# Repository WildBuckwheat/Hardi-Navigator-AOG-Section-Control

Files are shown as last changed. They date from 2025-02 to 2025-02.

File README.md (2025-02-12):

# Note

This project is a work in progress. Progress notes are shared below.

# Hardi-Navigator-AOG-Section-Control

 A PCB that adds AgOpenGPS section and rate control functionality to a Hardi Navigator 3000 trailed sprayer. This PCB replaces a PCB installed on the sprayer from the factory. No cutting of wires is required to install the new PCB and the sprayer can quickly be reverted to factory operation. Based very heavily on SK21's RC15 PCB.

 ## The Sprayer

 The sprayer is a Hardi Navigator 3000. This sprayer is generally by a John Deere 7410 tractor equipped with an AgOpenGPS guidance system. In the past this tractor was equipped with a Trimble CFX-750 and the Hardi JobCom connection was used for automatic section control. Since upgrading to AgOpenGPS the sections have been controlled manually. The intent of this project is to regain automatic section control.

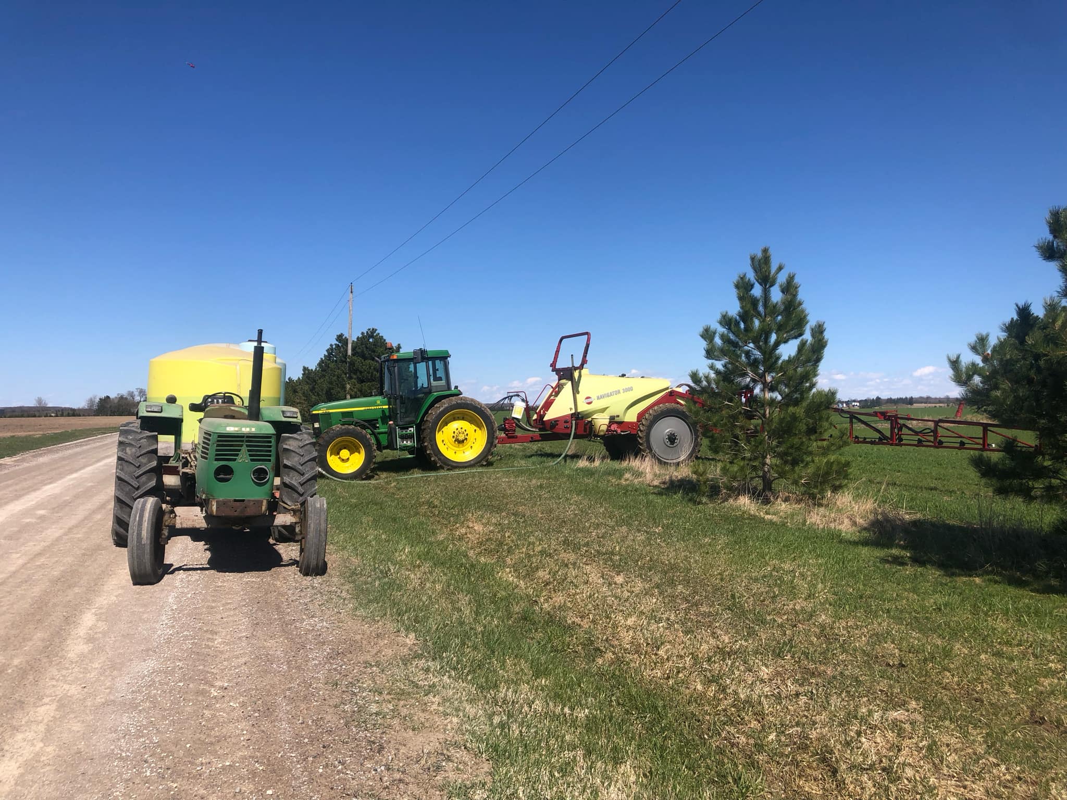
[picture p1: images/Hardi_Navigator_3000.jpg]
Hardi Navigator 3000
  

 The sprayer is equipped with a 90' eagle boom and 6 section valves. The 6 section valves are of the EVC type, utilizing a DC motor to direct flow between the boom and tank return.

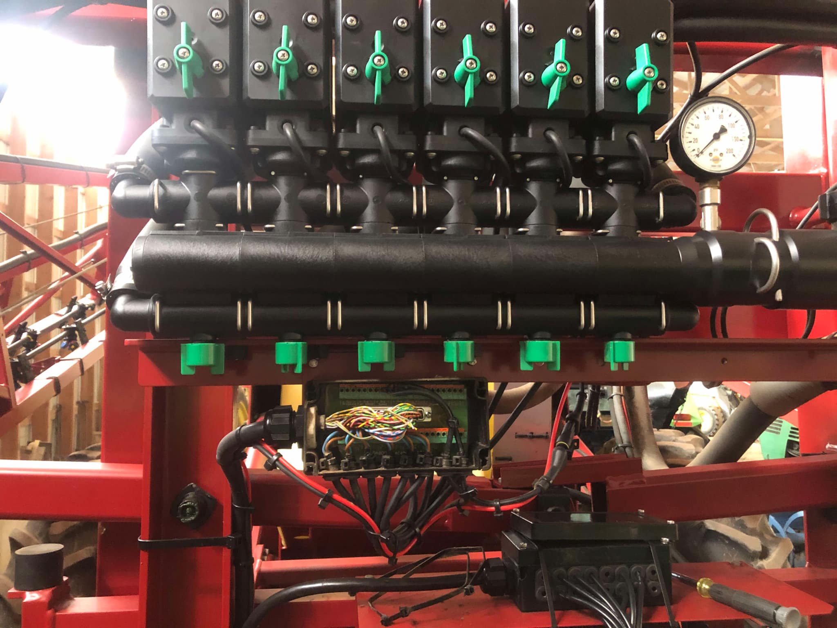
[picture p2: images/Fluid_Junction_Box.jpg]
Section Valves
 

 In cab control is through an HC5500 controller and Spray II controller. The HC5500 offers rate control while the Spray II controller offers manual section control and manual flow override.

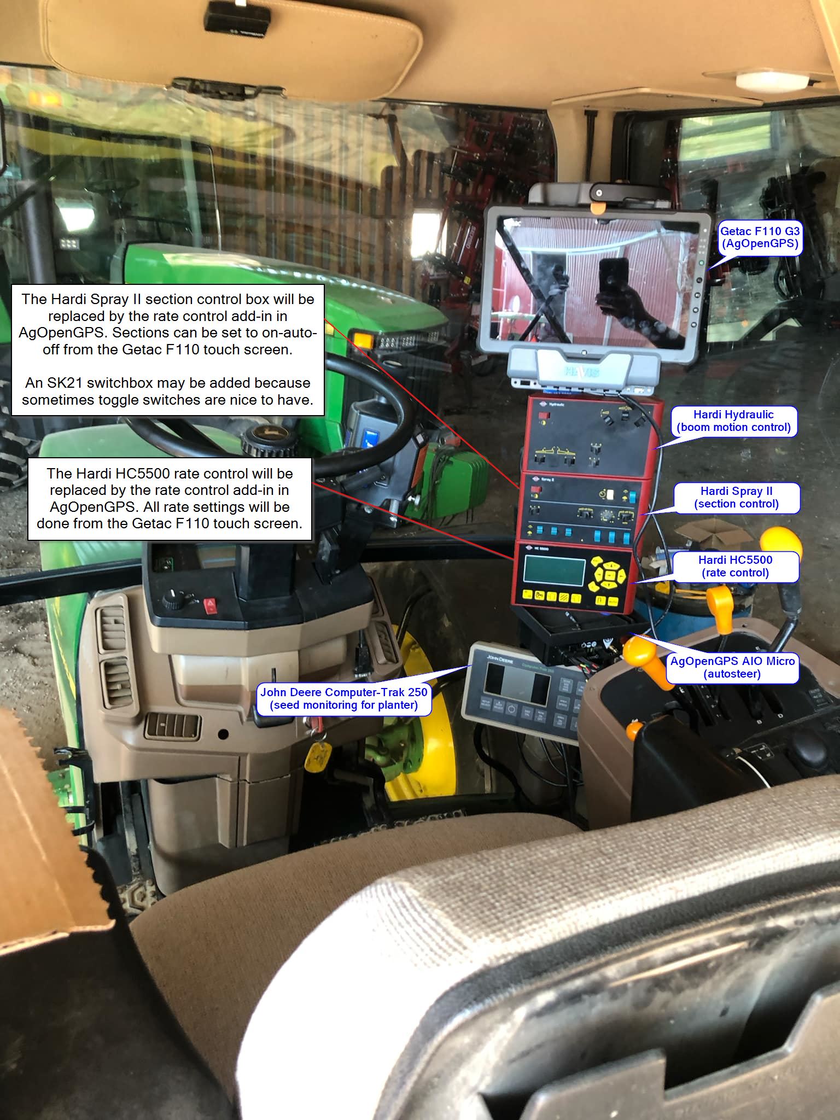
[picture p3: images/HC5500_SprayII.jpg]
HC5500 and Spray II control boxes mounted in 7410 cab Cab controls
  

 The sprayer is equipped with a Hardi JobCom PCB. This JobCom PCB is an upgrade PCB offered by Hardi which allows an external GPS system (Trimble, AgLeader, etc) to control the sections and rate via a serial connection to the HC5500. The JobCom PCB replaced the originally equipped Hardi Break-out PCB, a much simpler PCB with no microcontroller. While this project is underway I plan to leave the JobCom PCB installed in the sprayer and to study the Break-out PCB closely on my lab bench.

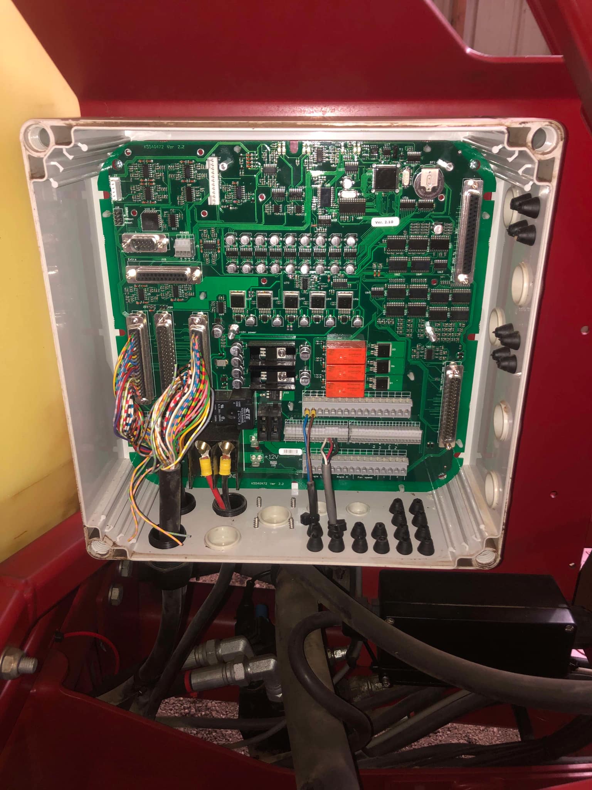
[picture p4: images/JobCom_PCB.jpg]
JobCom PCB
  

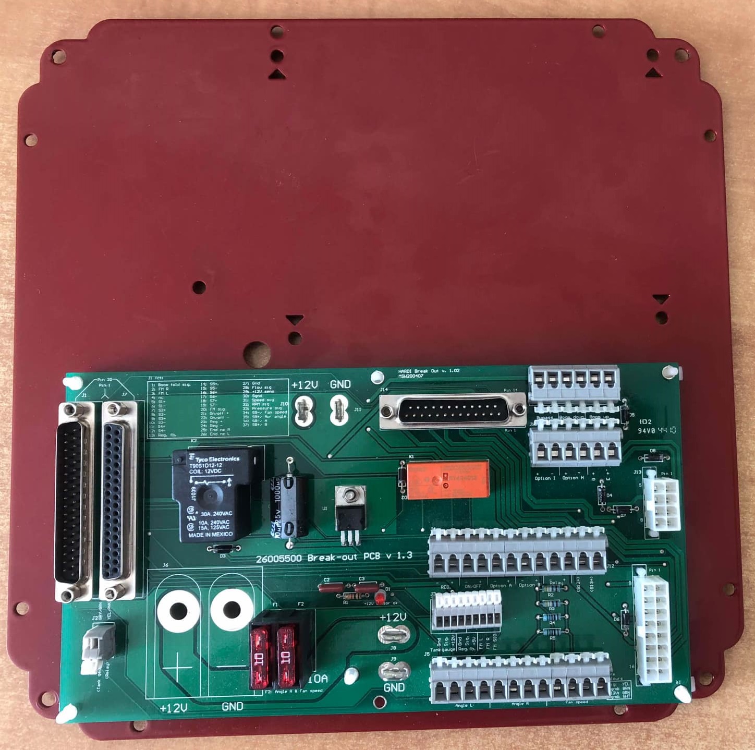
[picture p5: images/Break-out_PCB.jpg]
Break-out PCB
  

## The upgrade paths

I have thought of many ways to add AgOpenGPS section control to this sprayer.

My preferred path was to decode the serial protocol between the JobCom/HC5500 and Trimble CFX-750 (with VRA unlock). After taking several serial logs I was able to see patterns that matched the section control, but I was ultimately unable to decode the handshaking required (bi-directional connection). I snooped tx and rx simultaneously with separate single circuits, the data incoming to windows did not always align between the two connection. Perhaps with a better serial snooper I may have made more progres.

There can be found on the internet similar sprayers with AgOpenGPS section control added. The installations all involve relays and/or cutting wires. Cutting wires is something that I do not wish to do. I want to be able to return the sprayer to it's original condition quickly with minimal effort.

Ultimately the path that I have decided on is to take an existing project, [SK21's RC15 control board](https://github.com/SK21/AOG_RC), and to modify the project to suit my own needs.

## SK21 RC15

SK21 has developed the RC15 rate and section control . It has the following features.

- uses an ESP32 with wifi communication
- optionally a W5500 Ethernet Module can be added
- mostly surface mount parts
- can control two rates and 7-14 sections
- (2) DRV8870 motor drivers with reversible outputs for rates
- (7) DRV8870 motor drivers for either 7 reversible (motorized ball valve) outputs or 14 single ended (high or low) section outputs
- (4) 5V analog inputs (or 2 differential inputs)
- (2) optically isolated digital (rate/pulse) inputs, up to 12V
- RS485 chip & header
- 3.3V I2C header
- supports optional external RelayDriver5 I2C board
- connections through ampseal plug

A render of the SK21 RC15 PCB below

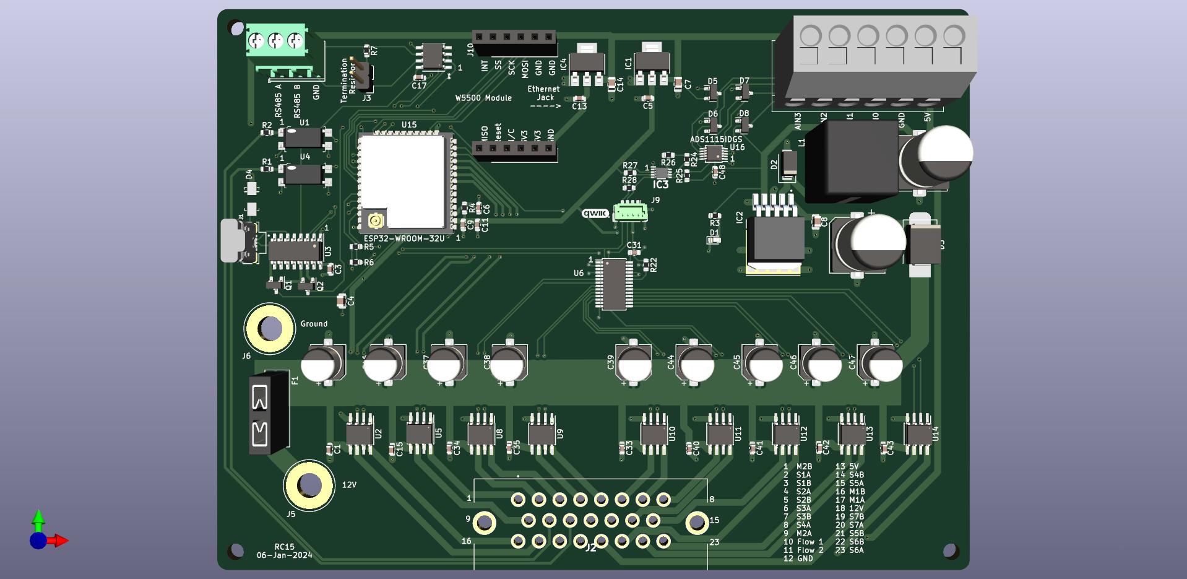
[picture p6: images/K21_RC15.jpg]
SK21 RC15


My needs are as described below
- 6 reversible (motorized ball valve) outputs
- 1 reversible output for rate control
- 1 12v input for rate
- wifi
- ethernet
- female db37 plug connection for valves and flow meter
- screw terminal or similar connection for regulator
- a very specific mounting pattern to fit in the control box
- input power via ring terminals

If the K21 RC15 was a different shape with different plugs then it would be ideal for this application. As a bonus, the firmware portion is already completed, the AgOpenGPS integration (through the rate control app) is already completed, the HC5500 and Spray II control boxes will be redundant, and the system will be capable of variable rate.

It should be straight forward to edit the SK21 RC15 schematic to add the plugs required, and then to create a custom PCB routing to create the required form factor.

## Data Collection - JobCom/Break-out PCB

The JobCom or Break-out PCB connects to the HC5500 and Spray II control boxes via a db37 connector. The new board will not utilize this connection of the HC5500/Spray II boxes. Still this connection is usefull, as the pinout is described both in the PCB silkscreen as well as in the Hardi manual.

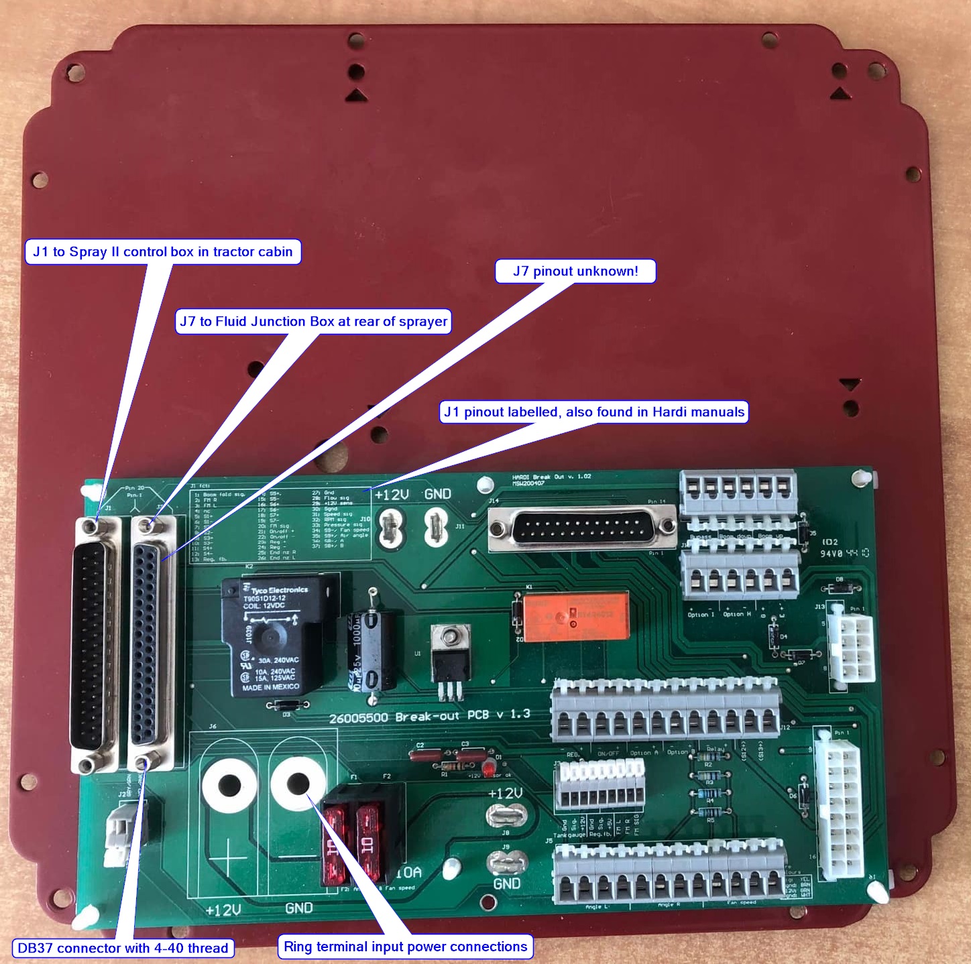
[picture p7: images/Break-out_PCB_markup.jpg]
Break-out PCB


The power connection to both the JobCom and Break-out PCB boards is quite interesting. Ring terminals are bolted to the board where bare copper is exposed.

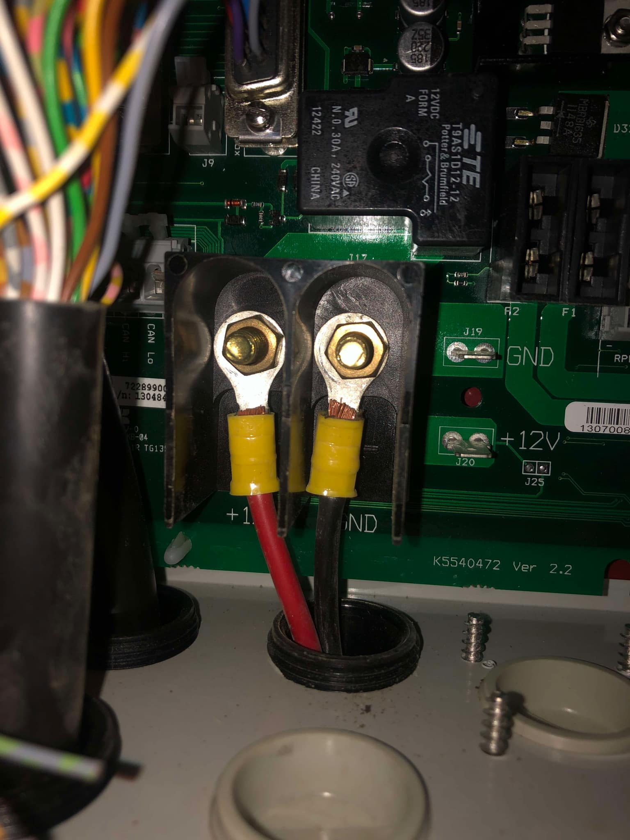
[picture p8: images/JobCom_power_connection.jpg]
JobCom Power Connection


The JobCom/Break-out PCB boards connect to the flow regulator with screwless terminals blocks. In my case there is also a connection to a foam marker harness. My sprayer is not equipped with foam markers and the harness appears to be dealer fabricated. I plan to remove this harness as it serves no purpose.

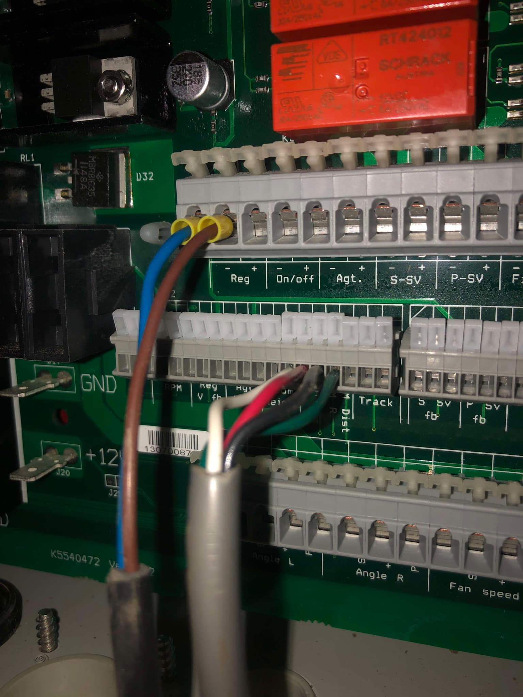
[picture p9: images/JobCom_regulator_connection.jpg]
JobCom Regulator Connection


What is of most interest is the DB37 connector that connects via cable to the Fluid Junction Box at the rear of the sprayer. Unfortunately the pinout at this connector does not appear to be described in any Hardi manual.

Break-out PCB

## Data Collection - Fluid Junction Box Cable

At the rear of the sprayer exists the Fluid Junction Box. Connected to the Fluid Junction Box are the 6 section valves, the flow meter, and the wheel speed sensor. The cable does not appear to have a direct 1-1 pinout.

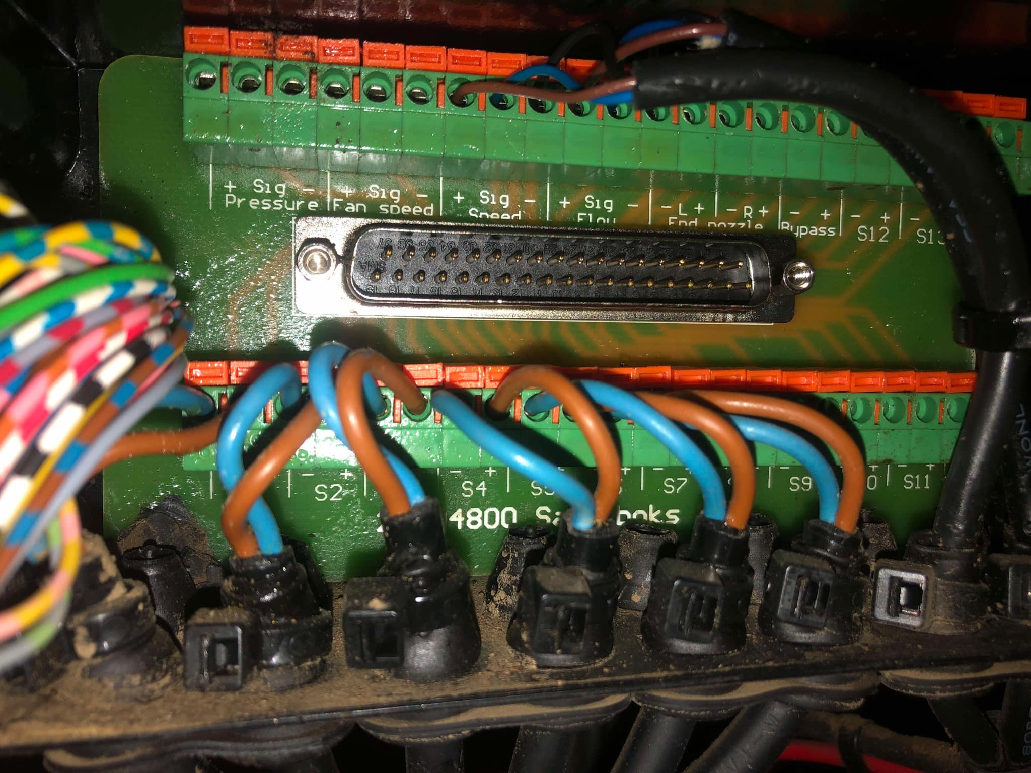
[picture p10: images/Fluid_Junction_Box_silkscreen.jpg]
Fluid Junction Box


## Data Collection - The missing pinout

The db37 to Fluid Junction Box connector pinout is crucial to know for the project to proceed. Through continuity tests between the connector in question and the labelled db37 to HC5500/Spray II connector I was able to determine much of the pinout. Some further continuity tests between the Fluid Junction Box and the connector were performed to verify the results. The secondary Fluid Junction Box tests were more troublesome to perform so not every pin was tested, but the results were as expected.

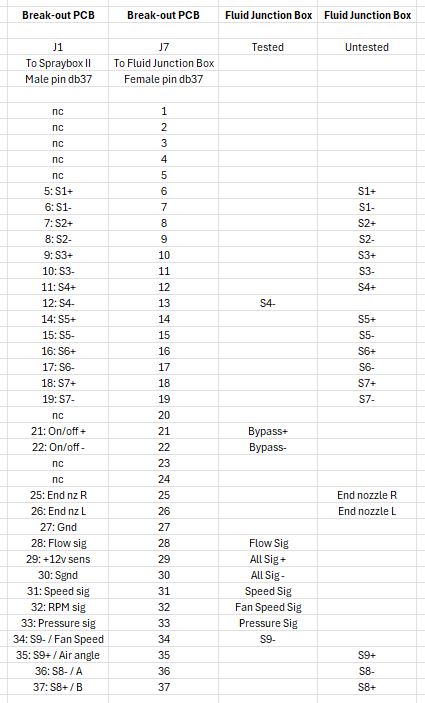
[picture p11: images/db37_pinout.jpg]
DB37 Pinout


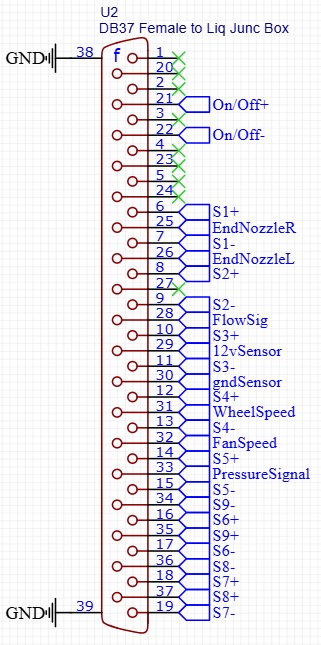
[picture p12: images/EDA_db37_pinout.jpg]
DB37 Pinout


# Data Collection - The Red Mounting Plate

Ideally the new PCB could mount in a similar method to the JobCom or Break-out PCB. Those PCBs mount using plastic standoffs to a red steel plate. It appears possible to mount both the Break-out PCB and the new board simultaneously without needing to drill any new holes. Leaving the Break-out PCB installed (disconnected) will make it very simple to bring the sprayer back to factory condition.

The red steel mounting plate was modelled in CAD so that a dxf could be imported into the EDA.

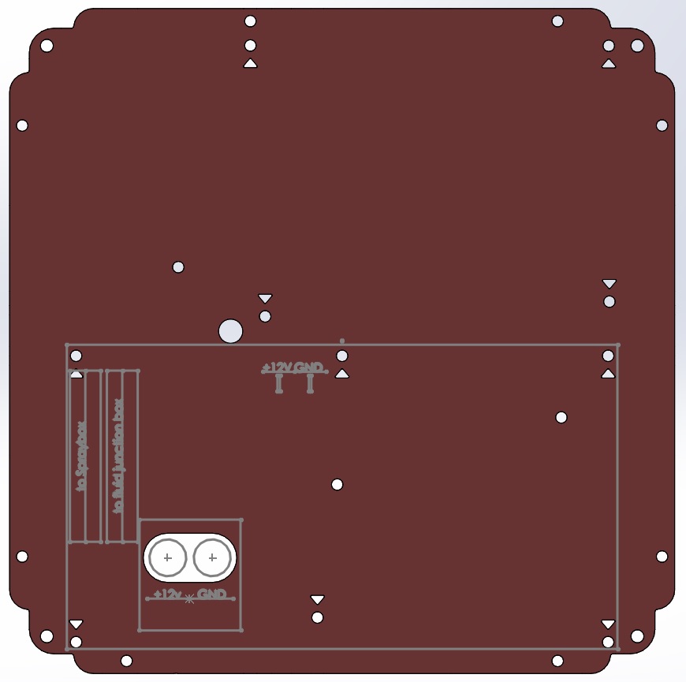
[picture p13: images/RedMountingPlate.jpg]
Mounting Plate


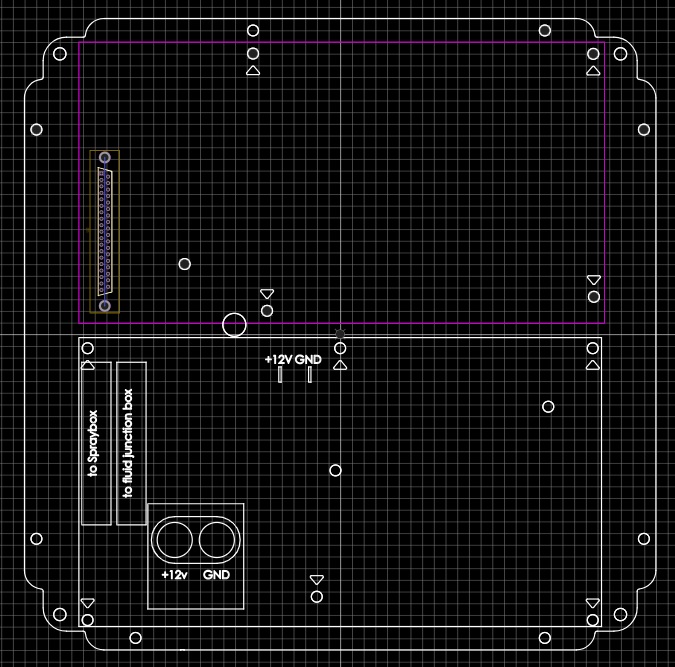
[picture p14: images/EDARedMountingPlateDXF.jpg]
Mounting Plate


# Data Collection - PCB Standoff

The steel plate has a thickness of 1.80mm (0.071") with 4.63mm (0.182") diameter mounting holes. The Break-out PCB has a thickness of 1.66mm (0.065") with 3.80mm (0.150") diameter mounting holes. The distance between the steel mounting plate and the PCB is 6.35mm (0.25").

The plastic standoffs appear to be Keystone 8808 which is readily available from Digikey and the likes https://www.digikey.ca/en/products/detail/keystone-electronics/8803/317140

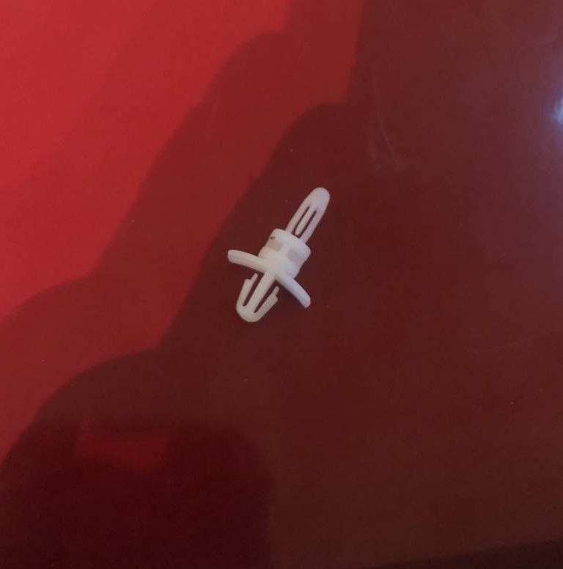
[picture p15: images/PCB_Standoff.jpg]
PCB Standoff

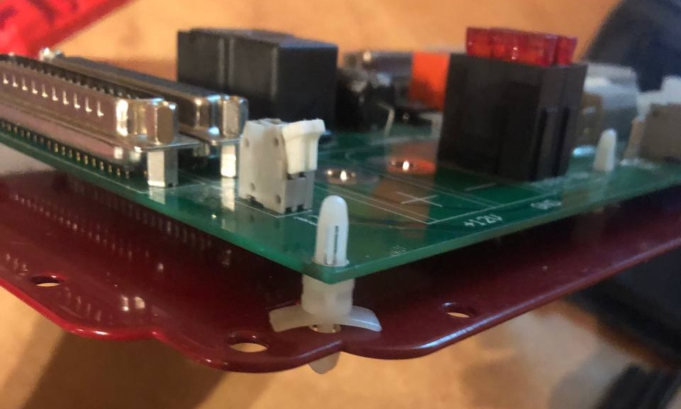
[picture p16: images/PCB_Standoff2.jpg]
PCB Standoff

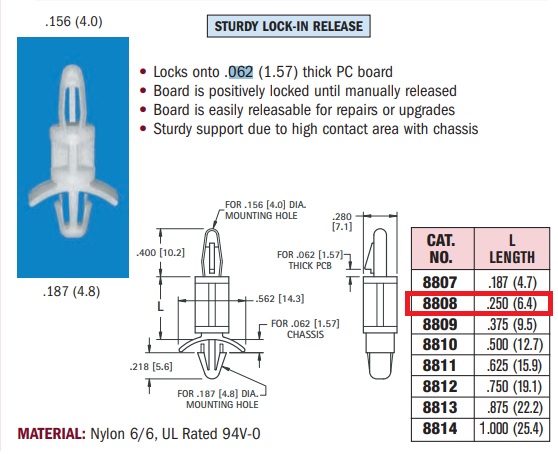
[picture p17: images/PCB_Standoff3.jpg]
PCB Standoff


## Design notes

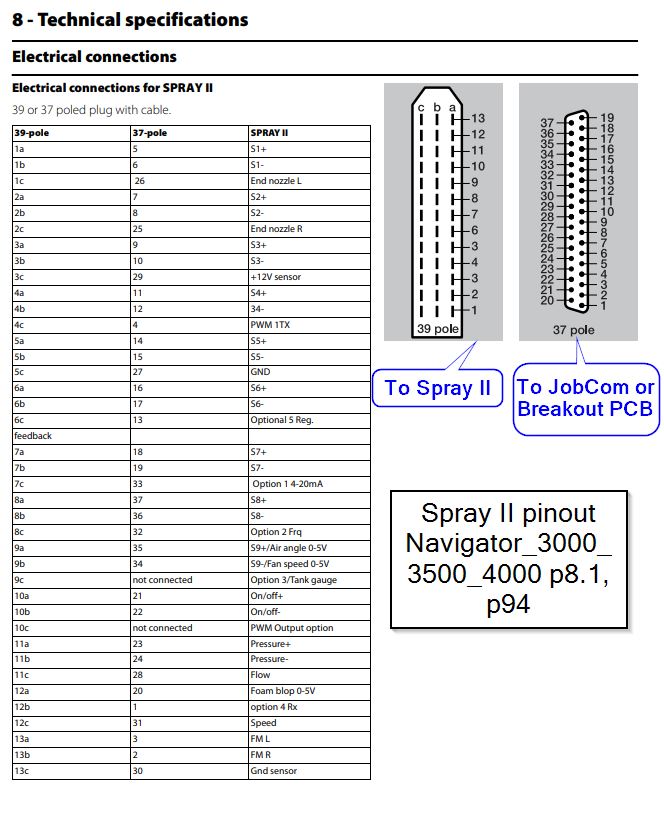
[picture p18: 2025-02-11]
Hardi Manuals/Spray II Pinout.jpg

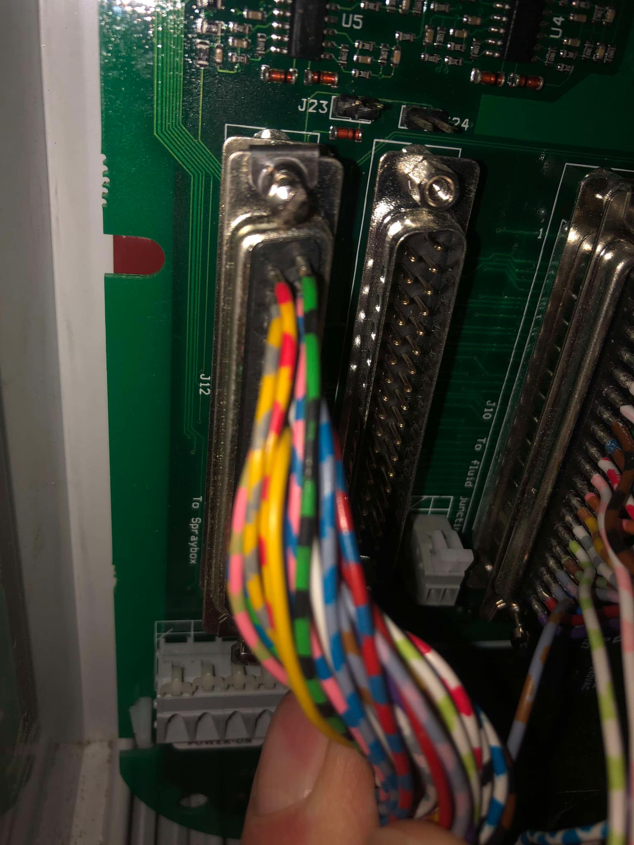
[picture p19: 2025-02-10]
images/JobCom db37 to spraybox.jpg

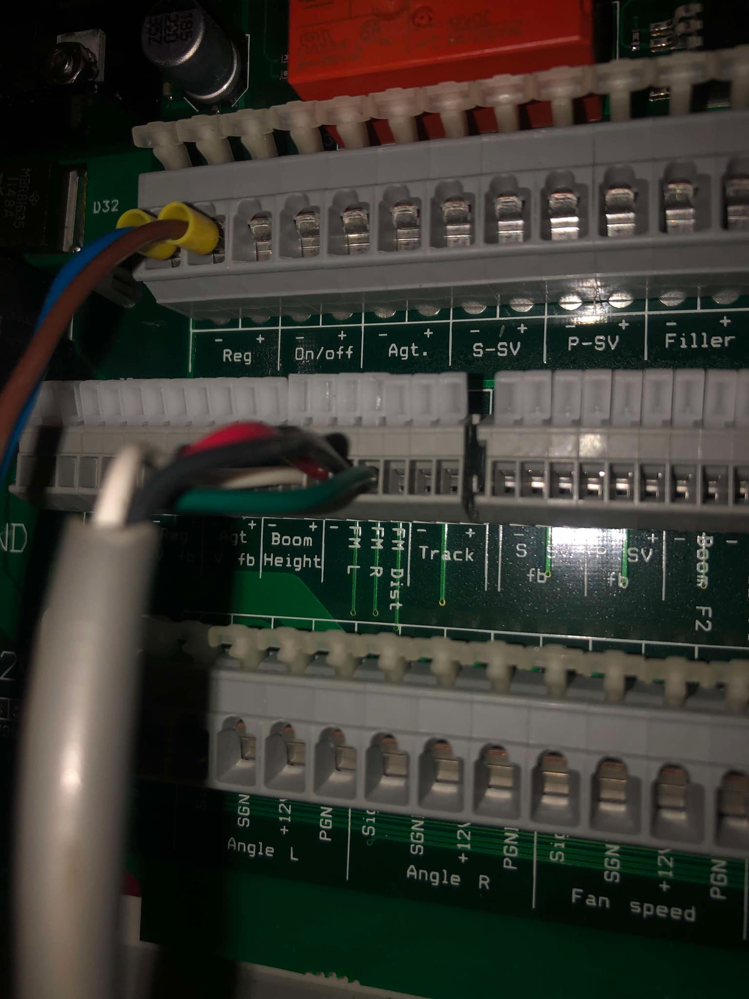
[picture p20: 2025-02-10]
images/JobCom FM connection.jpg

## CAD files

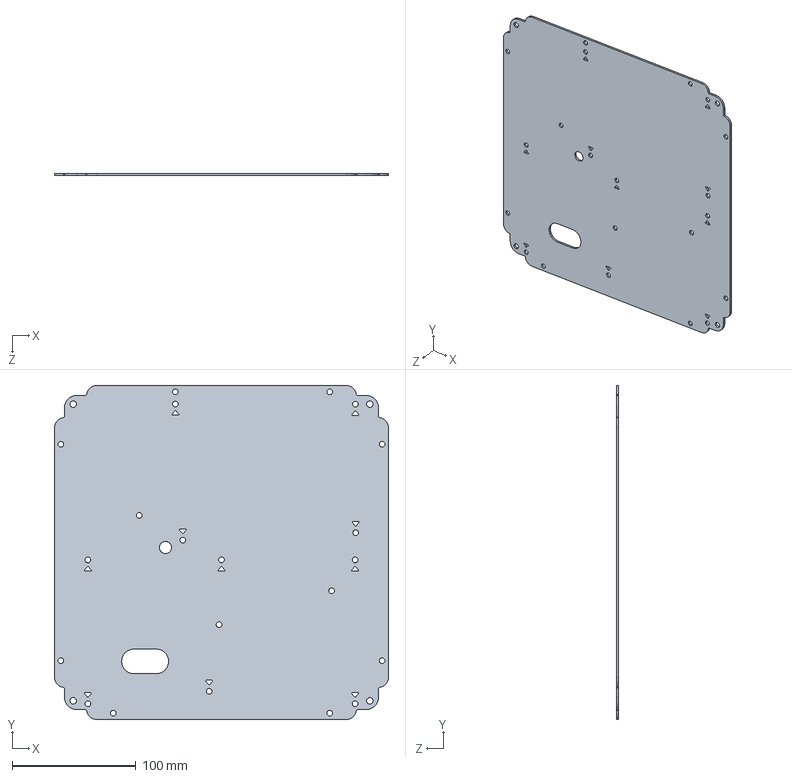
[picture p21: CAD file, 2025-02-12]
CAD/RedMountingPlate.SLDPRT
270.0 x 270.0 x 2.00 mm

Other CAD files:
CAD/RedMountingPlate.DXF
CAD/RedMountingPlate.SLDDRW
CAD/RedMountingPlate.STL

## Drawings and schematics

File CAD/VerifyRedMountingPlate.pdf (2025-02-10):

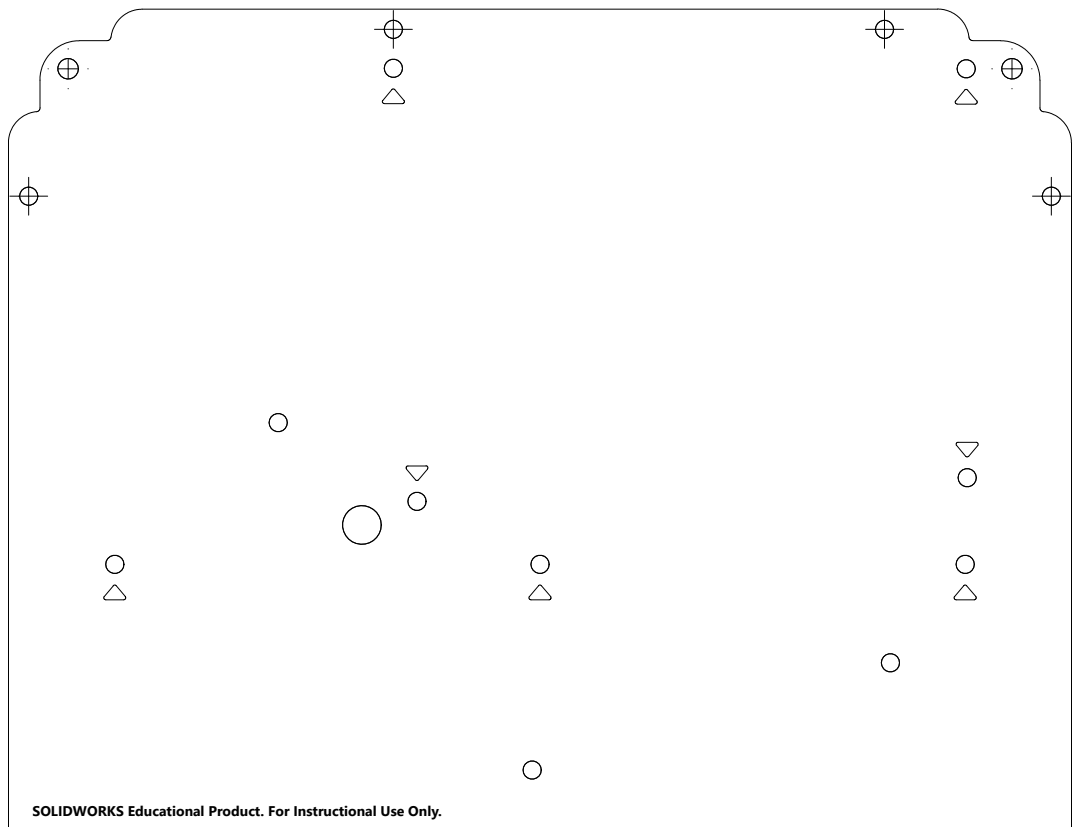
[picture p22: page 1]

SOLIDWORKS Educational Product. For Instructional Use Only.

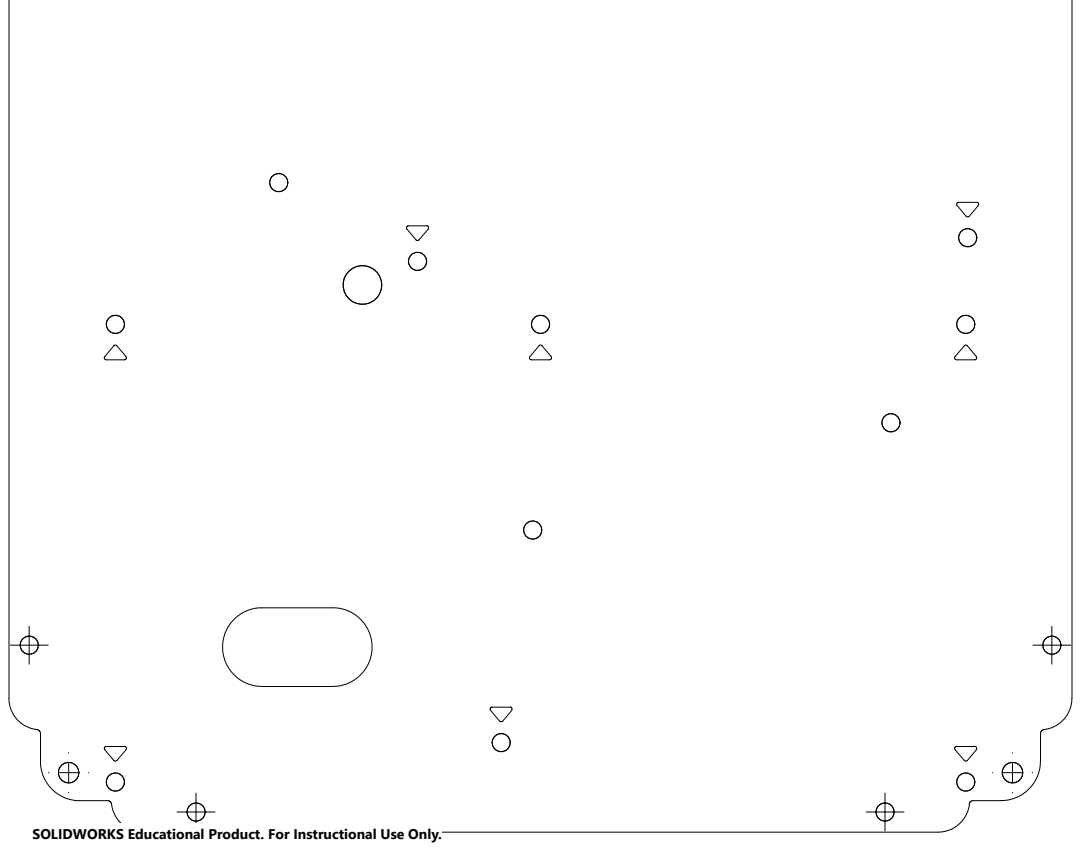
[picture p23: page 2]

SOLIDWORKS Educational Product. For Instructional Use Only.

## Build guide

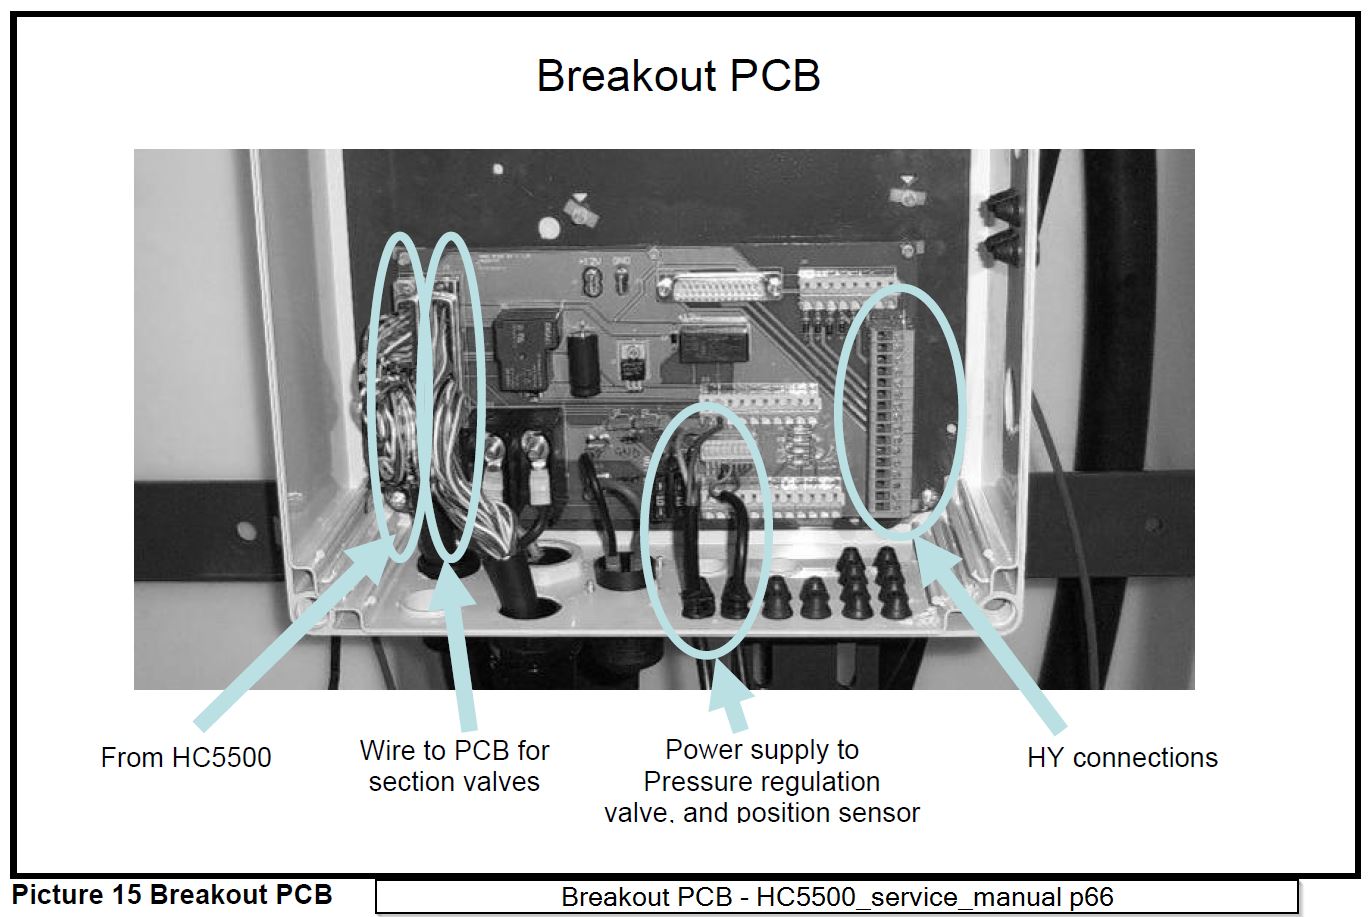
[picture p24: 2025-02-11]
Hardi Manuals/Breakout PCB - HC5500_service_manual_page66.jpg

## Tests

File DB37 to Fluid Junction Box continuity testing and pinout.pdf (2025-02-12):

DB37 to Fluid Junction Box Pinout

There exists a db37 to db37 cable between the JobCom/Break-out PCB and the Fluid Junction Box The cable does not appear to be a straight pass through
We need to know the pinout of this cable's db37 that connects to the JobCom/Break-out PCB Unfortunately I am unable to locate such a pinout in any documentation

First I performed a simple continuity test between J1 (has a labelled pinout) and J7 on the Break-out PCB Then I performed continuity tests between the Fluid Junction Box and the JobCom/Break-out PCB side db37 Not every Fluid Junction Box connection was tested, the process was tedious and all results were as expected The only used connections in my Fluid Junction Box are S1 - S6, the wheel speed sensor, and the flow sensor

From this information the required DB37 pinout is obtained

Break-out PCB | Break-out PCB | Fluid Junction Box Fluid Junction Box
J1 | J7 | Tested | Untested
To Spraybox II | To Fluid Junction Box
Male pin db37 | Female pin db37
nc | 1
nc | 2
nc | 3
nc | 4
nc | 5
5: S1+ | 6 | | S1+
6: S1- | 7 | | S1-
7: S2+ | 8 | | S2+
8: S2- | 9 | | S2-
9: S3+ | 10 | | S3+
10: S3- | 11 | | S3-
11: S4+ | 12 | | S4+
12: S4- | 13 | S4-
14: S5+ | 14 | | S5+
15: S5- | 15 | | S5-
16: S6+ | 16 | | S6+
17: S6- | 17 | | S6-
18: S7+ | 18 | | S7+
19: S7- | 19 | | S7-
nc | 20
21: On/off + | 21 | Bypass+
22: On/off - | 22 | Bypass-
nc | 23
nc | 24
25: End nz R | 25 | | End nozzle R
26: End nz L | 26 | | End nozzle L
27: Gnd | 27
28: Flow sig | 28 | Flow Sig
29: +12v sens | 29 | All Sig +
30: Sgnd | 30 | All Sig -
31: Speed sig | 31 | Speed Sig
32: RPM sig | 32 | Fan Speed Sig
33: Pressure sig | 33 | Pressure Sig
34: S9- / Fan Speed | 34 | S9-
35: S9+ / Air angle | 35 | | S9+
36: S8- / A | 36 | | S8-
37: S8+ / B | 37 | | S8+

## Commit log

2025-02-10 add pictures
    [RedMountingPlate.DXF, RedMountingPlate.SLDDRW, RedMountingPlate.SLDPRT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]
2025-02-11 Add more pictures, manuals, Fluid Junction Box pinout
    [DB37 to Fluid Junction Box continuity testing and pinout.xlsx, RedMountingPlate.DXF, RedMountingPlate.SLDPRT]
